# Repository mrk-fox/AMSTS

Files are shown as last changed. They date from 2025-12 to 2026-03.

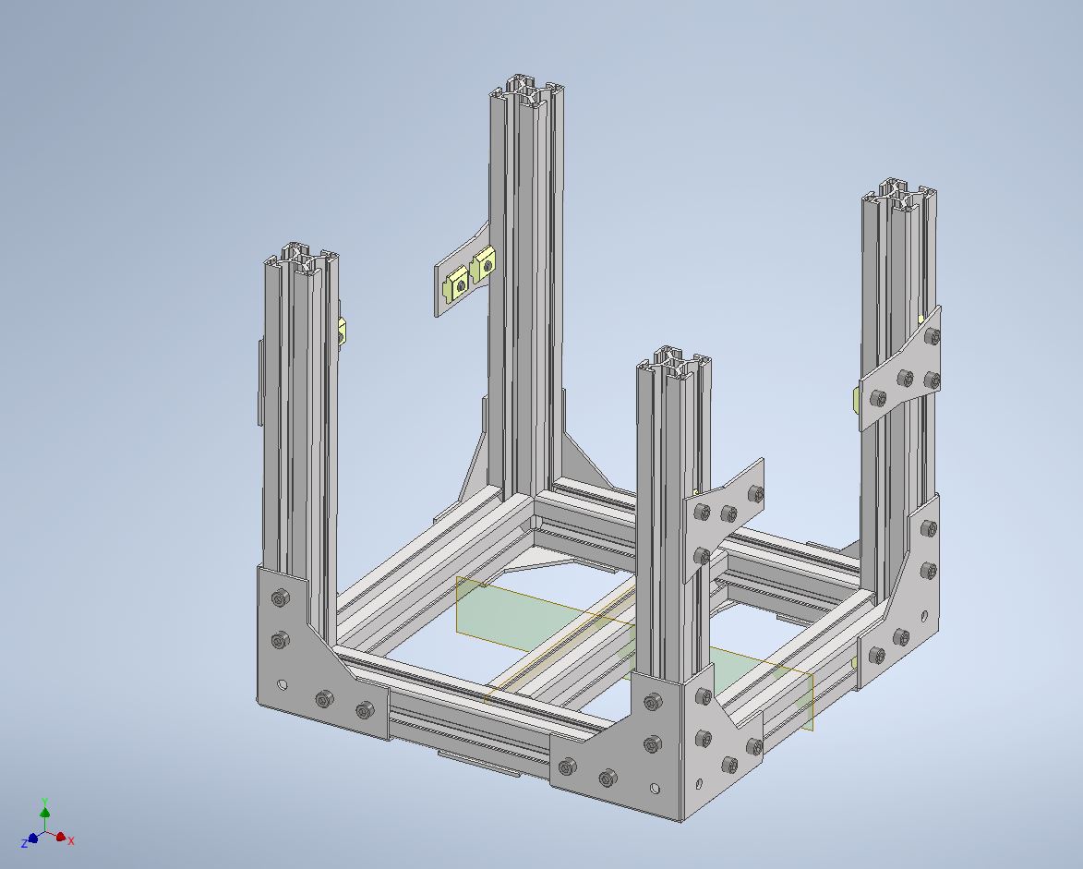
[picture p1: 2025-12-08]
hardware/Baseplate_with_verticals_and_semis.JPG

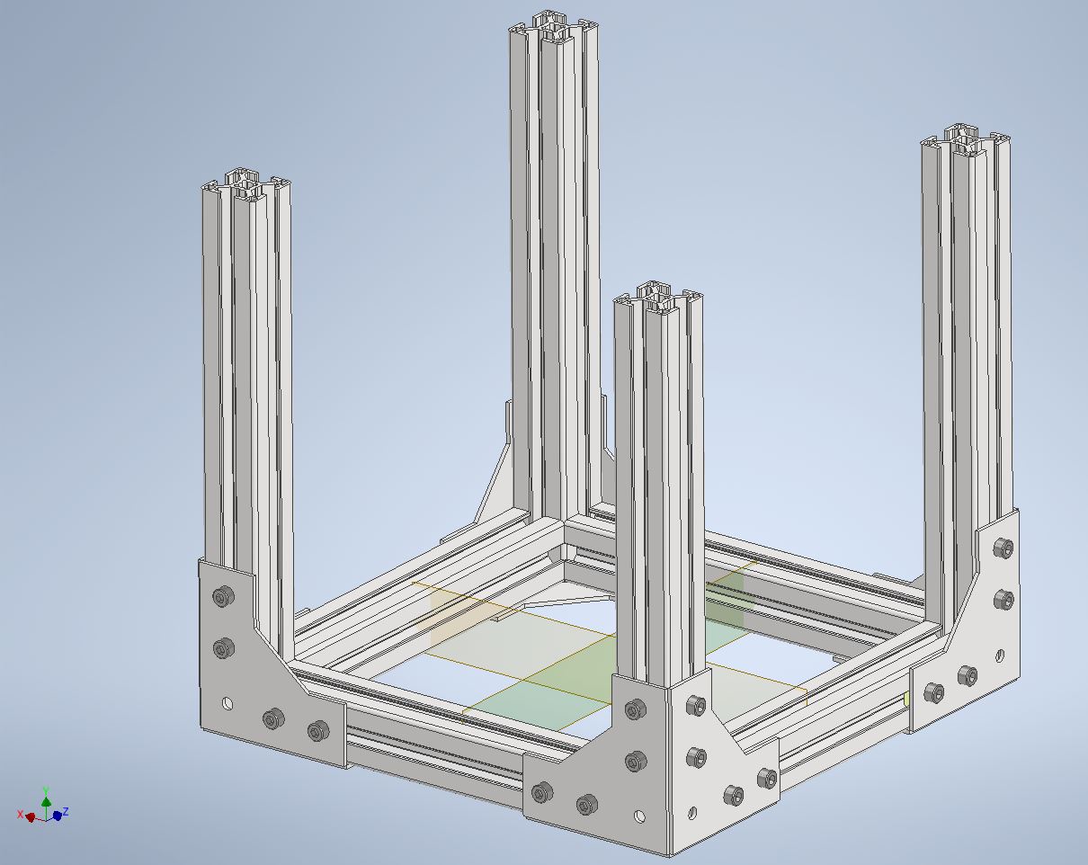
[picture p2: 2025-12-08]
hardware/Baseplate_with_verticals.JPG

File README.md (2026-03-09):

<h1 align="center">
  <br>
  
  <br>
  AMSTS
  <br>
</h1>

<h4 align="center">
A mobile satellite tracking system with a closed-loop system and high accuracy for yagi-uda antennas.
</h4>

<div align="center">

</div>

## Key Features

- **Closed loop system**
- **Magentometer alignment** for position-indipendant tracking
- **Polarization rotator** for correct polarization

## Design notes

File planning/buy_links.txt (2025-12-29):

https://www.ebay.de/itm/333755970393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
Linear Actuator

QMC5883L
Just that compass pse

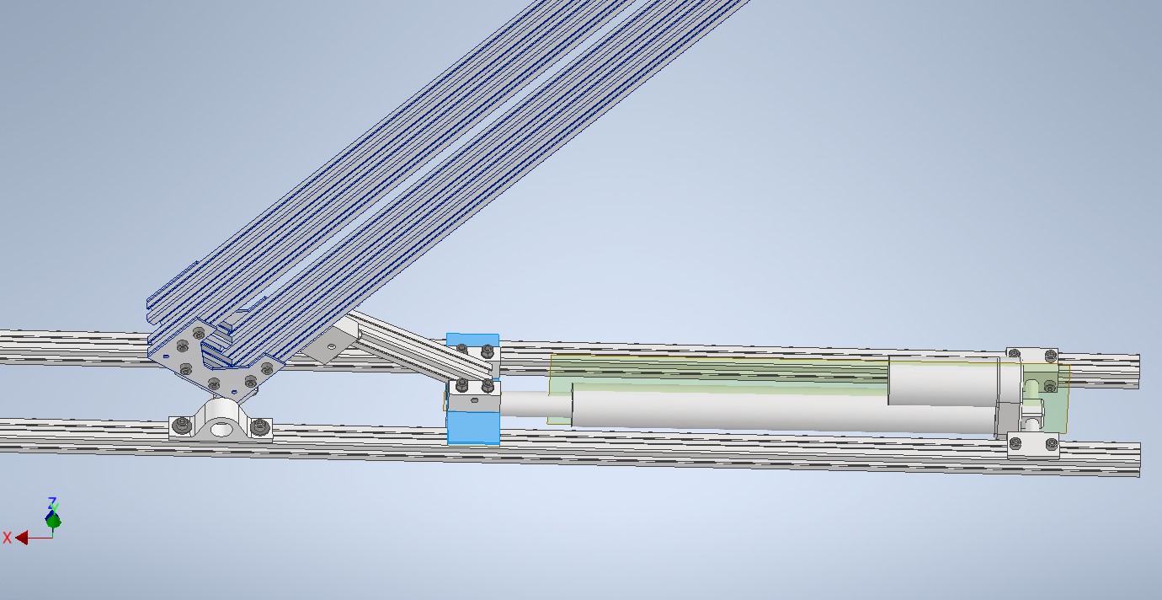
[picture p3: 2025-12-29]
hardware/v2_scissor.jpg

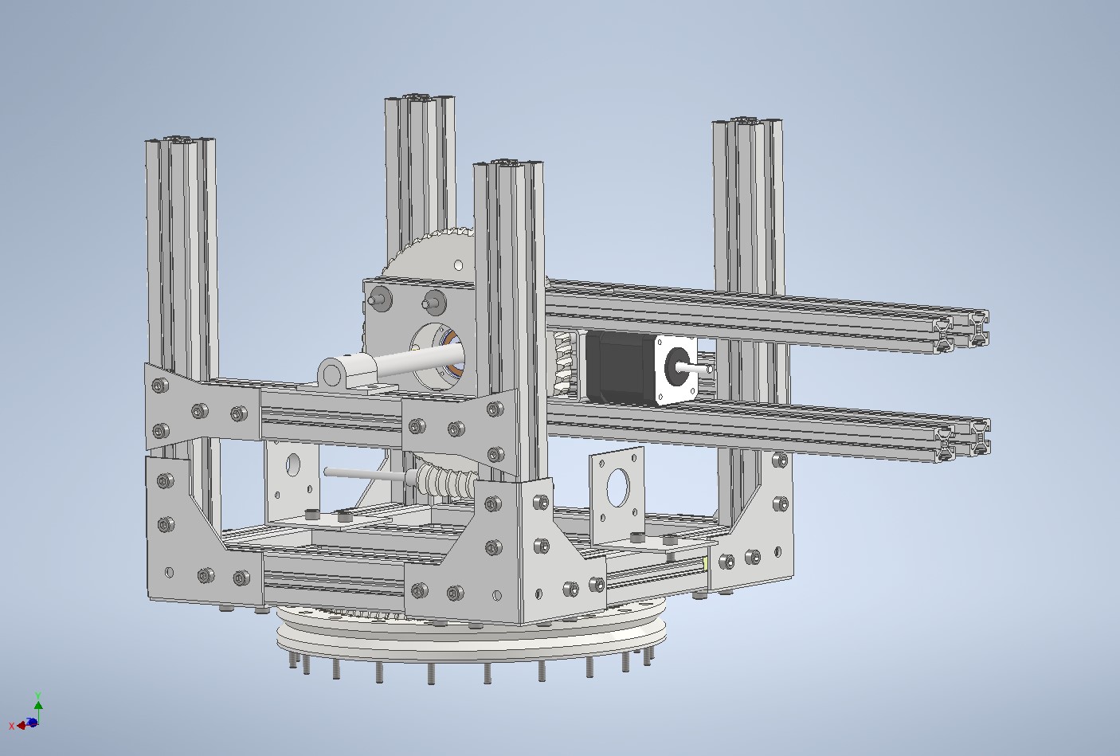
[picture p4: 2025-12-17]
hardware/Baseplate_with_gear_axBalks_BaseAz_motor.jpg

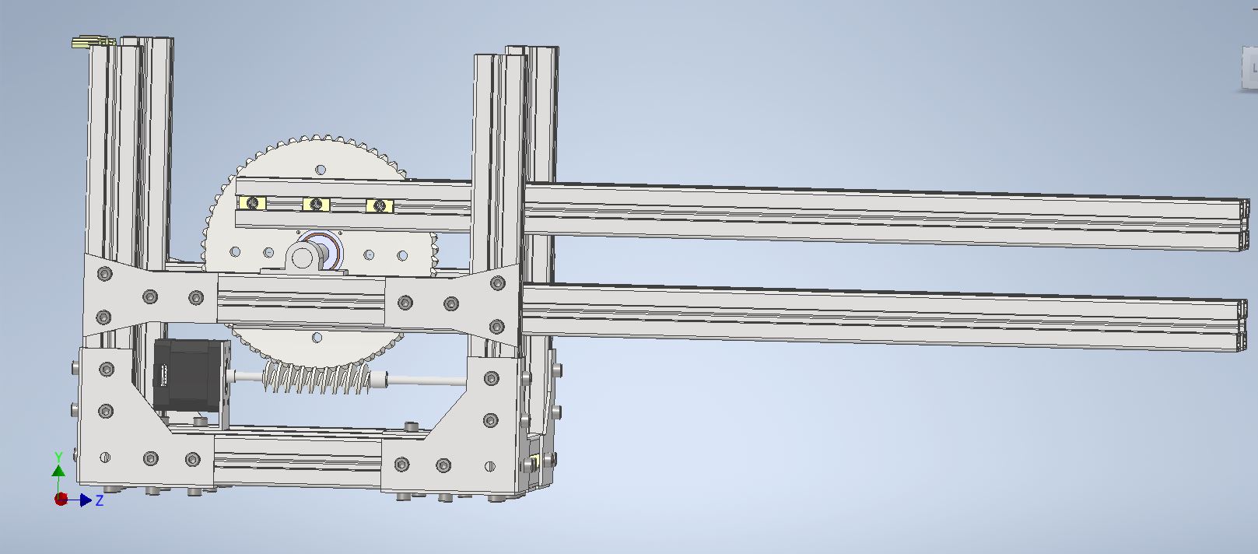
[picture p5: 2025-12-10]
hardware/Baseplate_with_gear_and_axBalks.JPG

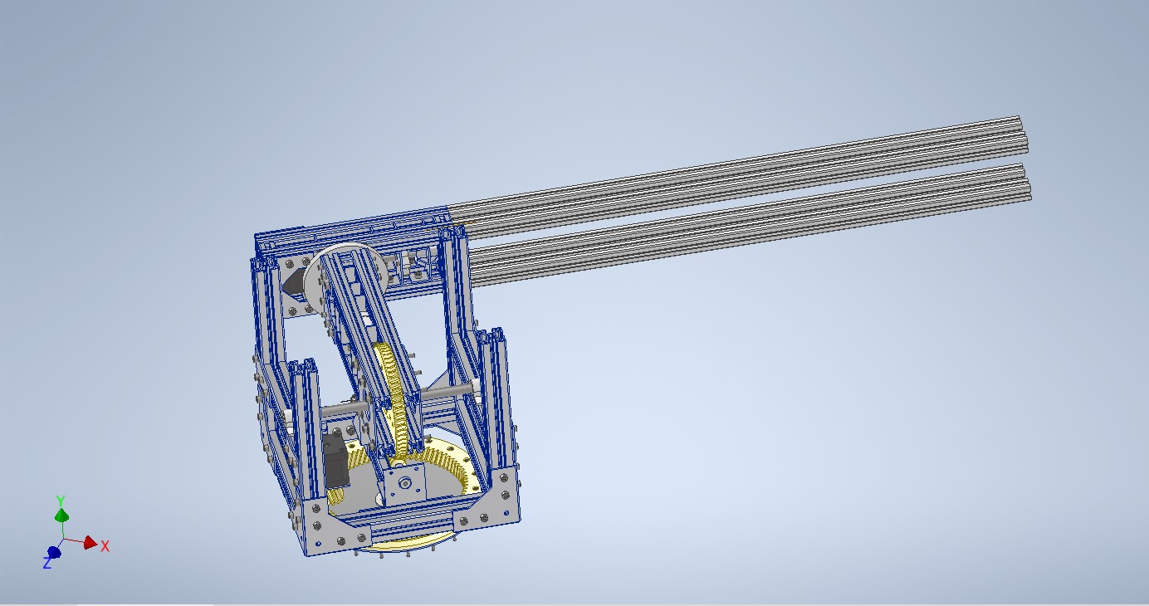
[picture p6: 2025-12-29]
hardware/ax4.jpg

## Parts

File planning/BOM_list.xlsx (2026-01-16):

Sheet: BOM
Item | Part Number | Thumbnail | BOM Structure | Unit QTY | QTY | Stock Number | Description | Length per piece | Total group
1 | 4x2020_ax4 |  | Normal | Each | 8 |  | 233,729mm 2020 | 233.729 | 1869.832 | Buy - Cut
2 | 4x2020_universal |  | Normal | Each | 2 |  | NEMA 17 Stepper Motor Holder |  | 0 | Let Produce - Drill - Bend
3 | 17HE19-2004S |  | Normal | Each | 2 |  | STEP AP214 |  | 0 | Buy
4 | 4x2020_universal_planetary |  | Normal | Each | 2 |  | NEMA 17 Planetary Holder |  | 0 | Let Produce - Drill - Bend
5 | EG17 shaft-2 |  | Normal | Each | 2 |  | Part of NEMA 17 Planetary |  | 0 | Buy
6 | nema17input flange |  | Normal | Each | 2 |  | Part of NEMA 17 Planetary |  | 0 | Buy
7 | input shaft |  | Normal | Each | 2 |  | Part of NEMA 17 Planetary |  | 0 | Buy
8 | ¦µ10circlip |  | Normal | Each | 2 |  | Part of NEMA 17 Planetary |  | 0 | Buy
9 | M3hexagon socket head cap screw |  | Normal | Each | 16 |  | Part of NEMA 17 Planetary |  | 0 | Buy
10 | 6801 |  | Normal | Each | 2 |  | 6801 bearing |  | 0 | Buy
11 | 4x2020_axis |  | Normal | Each | 2 |  | 8mm 4x2020 Axis |  | 0 | Buy - Weld - Drill - Thread
12 | 4x2020_blank |  | Normal | Each | 2 |  | AMT222D-V Encoder 4x2020 Holder |  | 0 | Let Produce - Drill - Bend
13 | AMT102-0512-I5000-5 |  | Normal | Each | 1 |  | AMT222D-V Encoder |  | 0 | Buy
14 | AS 1420 - 1973 - M3 x 16 |  | Purchased | Each | 4 |  | ISO metric hexagon socket head cap screws |  | 0 | Buy
15 | ISO 4032 - M2,5 |  | Purchased | Each | 4 |  | Hex Nut |  | 0 | Buy
16 | 4x2020_axis_end_bearings |  | Normal | Each | 2 |  | Double 628 Bearings holder |  | 0 | Let Produce - Drill - Bend - Weld
17 | 628_bearing |  | Normal | Each | 4 |  | 628 Bearing |  | 0 | Buy
18 | tnut_m5_2020 |  | Normal | Each | 161 |  | STEP AP214 |  | 0 | Buy
19 | ISO 4762 - M5 x 8 |  | Purchased | Each | 122 |  | Hexagon Socket Head Cap Screw |  | 0 | Buy
20 | 2020_4x2020_hz |  | Normal | Each | 8 |  | 14.112mm 2020 Profile | 14.112 | 112.896 | Buy - Cut
21 | 2020_4x2020_ve |  | Normal | Each | 10 |  | 48.3mm 2020 Profile | 48.3 | 483 | Buy - Cut
22 | Connect_u2020 |  | Normal | Each | 10 |  | U-Connector 2020 Profile |  | 0 | Let Produce
23 | m4x70_example |  | Normal | Each | 8 |  | M4x70mm screw |  | 0 | Buy - Weld - Drill - Thread
24 | DIN 9021 - 4,3 |  | Purchased | Each | 16 |  | Washer |  | 0 | Buy
25 | ANSI B18.2.4.2M - M4x0,7 |  | Purchased | Each | 8 |  | Metric Hex Nuts Styles 2 |  | 0 | Buy
26 | 4ax_plate_joint |  | Normal | Each | 1 |  | Az-El Deloder Plate |  | 0 | 3D Print
27 | DIN 920 - M5 x 10 |  | Purchased | Each | 6 |  | Slotted Pan Head Screw |  | 0 | Buy
28 | ax4_holder |  | Normal | Each | 1 |  | 4x2020 to 8mm Connctor |  | 0 | Let Produce (Buy - Cut - Drill) - Drill - Weld
29 | 2020_ax_connector |  | Normal | Each | 1 |  | 2020 to 8mm Connector |  | 0 | Let Produce (Buy - Cut - Drill) - Drill - Weld
30 | 2020_140 |  | Normal | Each | 1 |  | 140mm 2020 Profile | 140 | 140 | Buy - Cut
31 | 2020_700 |  | Normal | Each | 4 |  | 700mm 2020 Profile | 700 | 2800 | Buy - Cut
32 | H-Connector_2020 |  | Normal | Each | 2 |  | H-Connector 2020 Profiles |  | 0 | Let Produce
33 | 4x2020_subaxis |  | Normal | Each | 1 |  | 4x2020 8mm Axis Shaft |  | 0 | 3D Print
34 | DIN 9021 - 5,3 |  | Purchased | Each | 14 |  | Washer |  | 0 | Buy
35 | ISO 4762 - M5 x 10 |  | Purchased | Each | 16 |  | Hexagon Socket Head Cap Screw |  | 0 | Buy
36 | ISO 4762 - M4 x 8 |  | Purchased | Each | 1 |  | Hexagon Socket Head Cap Screw |  | 0 | Buy
37 | ISO 4762 - M5 x 12 |  | Purchased | Each | 8 |  | Hexagon Socket Head Cap Screw |  | 0 | Buy
38 | 8x7mm_spacer |  | Normal | Each | 2 |  | 8x7mm 8mm Axis Spacer |  | 0 | 3D Print
39 | 608 |  | Normal | Each | 2 |  | 608 Bearing |  | 0 | Buy
40 | base_axis_8mm_2020 |  | Normal | Each | 2 |  | Base Axis Holder |  | 0 | 3D Print
41 | 8x88_cylinder |  | Normal | Each | 1 |  | 8x88mm Axis |  | 0 | Buy - Cut
42 | 2020_1100 |  | Normal | Each | 2 |  | 1000mm 2020 Profile | 1000 | 2000 | Buy
43 | 2x2020_hor |  | Normal | Each | 2 |  | 68.112mm 2020 Profile | 68.112 | 136.224 | Buy - Cut
44 | 2020_108 |  | Normal | Each | 1 |  | 108.112mm 2020 Profile | 108.112 | 108.112 | Buy - Cut
45 | l-holder_2020 |  | Normal | Each | 6 |  | 2020 L-Connector |  | 0 | 3D Print
46 | l-holder_2020_spacer |  | Normal | Each | 1 |  | 2mm Plastic 2020 Spacer |  | 0 | 3D Print
47 | manual_locker |  | Normal | Each | 1 |  | Manual Locker Lower Part |  | 0 | Let Produce - Bend
48 | manual_locker_upoper |  | Normal | Each | 1 |  | Manual Locker Upper Part |  | 0 | Let Produce - Bend
49 | antenna_rad |  | Normal | Each | 2 |  | Antenna Holder Inner |  | 0 | 3D Print
50 | antenna_rad_outter |  | Normal | Each | 2 |  | Antenna Holder Outter |  | 0 | 3D Print
51 | ISO 4762 - M5 x 16 |  | Purchased | Each | 8 |  | Hexagon Socket Head Cap Screw |  | 0 | Buy
52 | bearing_stifts_antenna |  | Normal | Each | 2 |  |  |  | 0 | Buy - Cut - File
53 | gps_holder |  | Normal | Each | 1 |  | GPS Holder |  | 0 | 3D Print
54 | gps_lid |  | Normal | Each | 1 |  | GPS Holder Lid |  | 0 | 3D Print
55 | servo_holder |  | Normal | Each | 1 |  | DS-3240MG Servo Holder |  | 0 | 3D Print
56 | ISO 4762 - M5 x 20 |  | Purchased | Each | 2 |  | Hexagon Socket Head Cap Screw |  | 0 | Buy
57 | sk7_2 |  | Normal | Each | 1 |  | STEP AP214 |  | 0 | Buy
58 | Part4 |  | Normal | Each | 1 |  | DS-3240MG Servo |  | 0 | Buy
59 | counterweight-rod |  | Normal | Each | 1 |  | Counterweight Rod (8mm) |  | 0 | Buy - File - Drill - Cut
60 | DIN 9021 - 6,4 |  | Purchased | Each | 1 |  | Washer |  | 0 | Buy
61 | ISO 4762 - M6 x 10 |  | Purchased | Each | 1 |  | Hexagon Socket Head Cap Screw |  | 0 | Buy
62 | counterweight# |  | Normal | Each | 1 |  | Counterweight |  | 0 | Buy - Produce
63 | antenna_polarization_rot_conn |  | Normal | Each | 1 |  | 2020-to-Servo adapter |  | 0 | 3D Print
64 | ISO 4762 - M2 x 16 |  | Purchased | Each | 2 |  | Hexagon Socket Head Cap Screw |  | 0 | Buy
65 | ISO 4762 - M2 x 12 |  | Purchased | Each | 2 |  | Hexagon Socket Head Cap Screw |  | 0 | Buy
 |  |  |  |  |  |  |  | 2020 Length tot: | 7650.064

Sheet: Cost
id | Name | QTY | Price | Seller | Link | Priority
1 | 4x2020_raw | 8 | 72.79 € | Blexon AG | blexon.com | 1
2 | manual_locker_raw | 3 | x | Blexon AG | blexon.com | 2
3 | manual_locker_upper_raw | 3 | x | Blexon AG | blexon.com | 2 | Subsum for Seller: | 109.87 €
4 | AMT222D-V | 1 | 44.77 € | Mouser Electronics GmbH | eu.mouser.com | 1
5 | AMT-06C-1-036 | 1 | 29.52 € | Mouser Electronics GmbH | eu.mouser.com | 1
6 | Adafruit 6109 (A4988) | 2 | 11.96 € | Mouser Electronics GmbH | eu.mouser.com | 1
7 | Arduino MEGA 2560 A000067 | 1 | 38.33 € | Mouser Electronics GmbH | eu.mouser.com | 1 | Subsum for Seller: | 124.58 €
8 | 8000mm 2020 Profile | 4 | 78.56 € |  | eBay (https://www.ebay.de/itm/393996614124?chn=ps&_ul=DE&google_free_listing_action=view_item) | 1
9 | NEMA 17 1:50 PG | 2 | 67.89 € | StepperMotors | https://www.omc-stepperonline.com/ | 1
10 | NEMA 17 Stepper Motors | 2 | 18.60 € | StepperMotors | https://www.omc-stepperonline.com/ | 1
11 | DS-3240MG Servo | 1 | 22.99 € |  | eBay (https://www.ebay.de/itm/276703280300?chn=ps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) | 1
12
13
14 |  | Sum: | 385.41 €
15
16
17
18

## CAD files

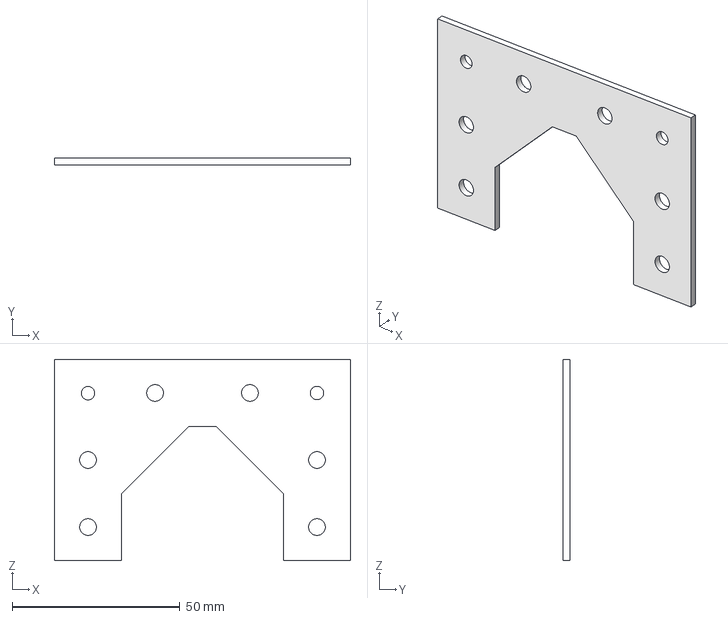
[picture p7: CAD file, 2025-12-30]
hardware/Connect_u2020_raw.stp
88.3 x 2.00 x 60.0 mm

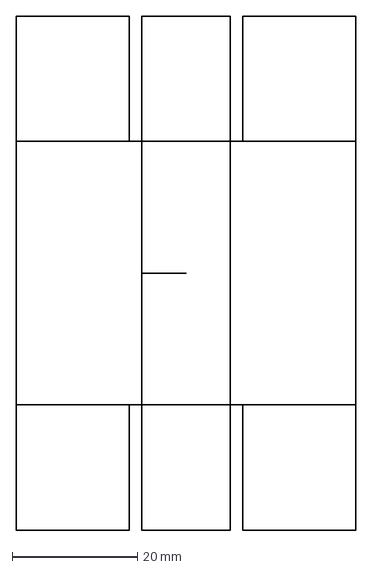
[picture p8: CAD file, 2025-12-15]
sketches/4x2020_universal_raw.dxf
54.1 x 82.0 mm

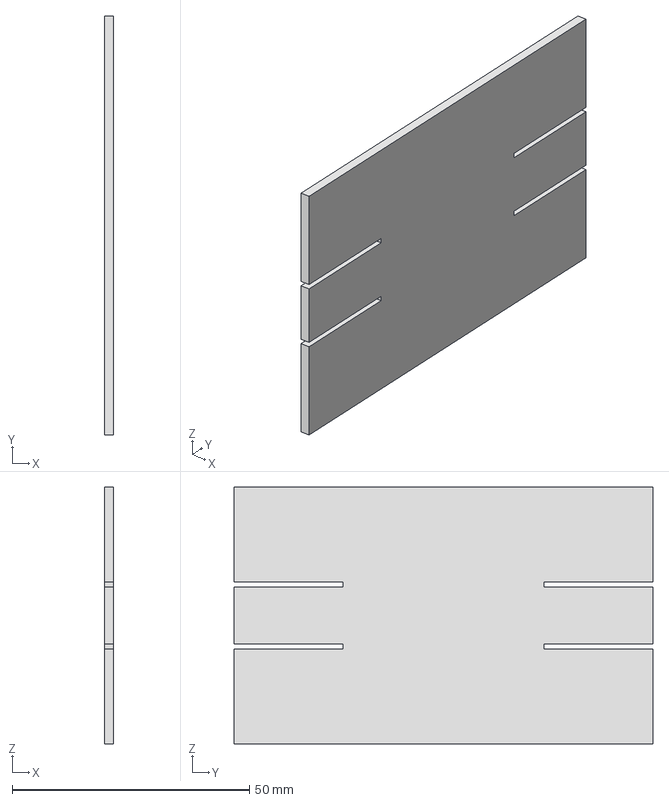
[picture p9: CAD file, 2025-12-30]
hardware/4x2020_raw.stp
2.00 x 88.3 x 54.1 mm

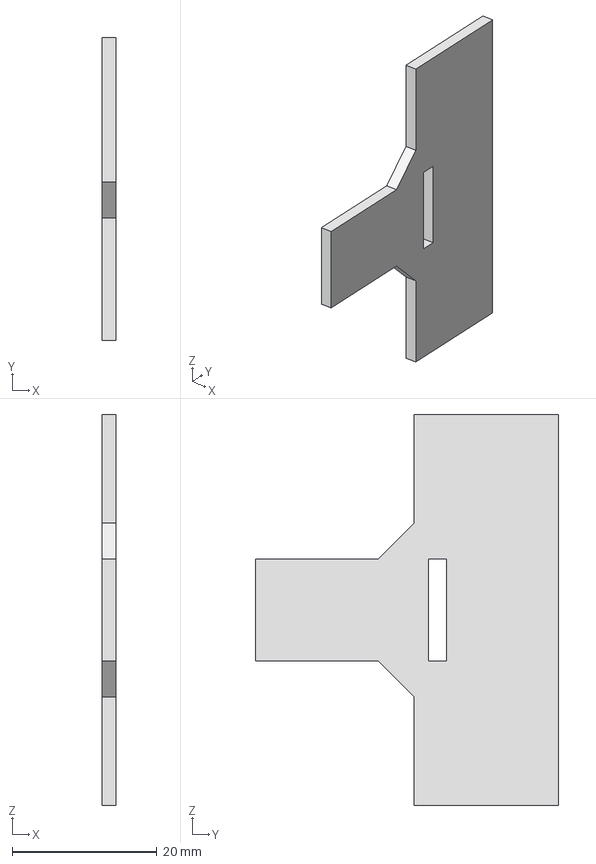
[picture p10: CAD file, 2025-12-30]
hardware/manual_locker_upper_raw.stp
2.00 x 42.0 x 54.1 mm

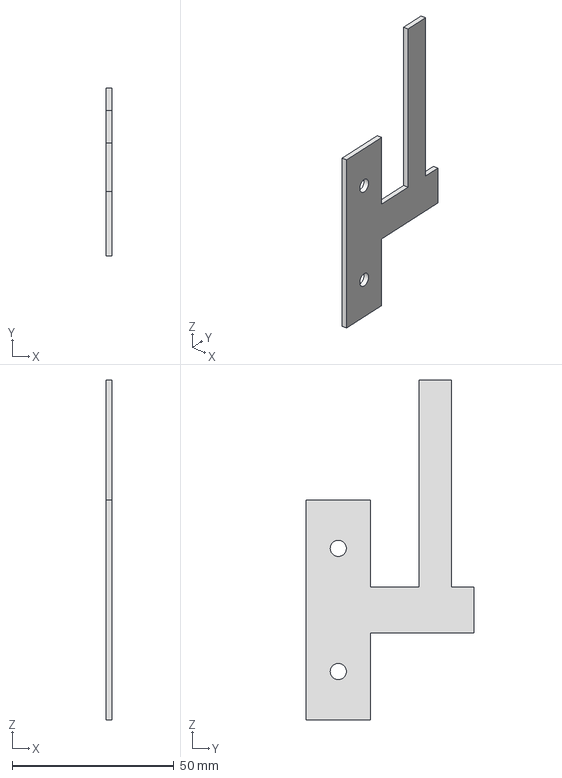
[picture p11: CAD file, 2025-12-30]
hardware/manual_locker_raw.stp
2.00 x 52.0 x 105.2 mm

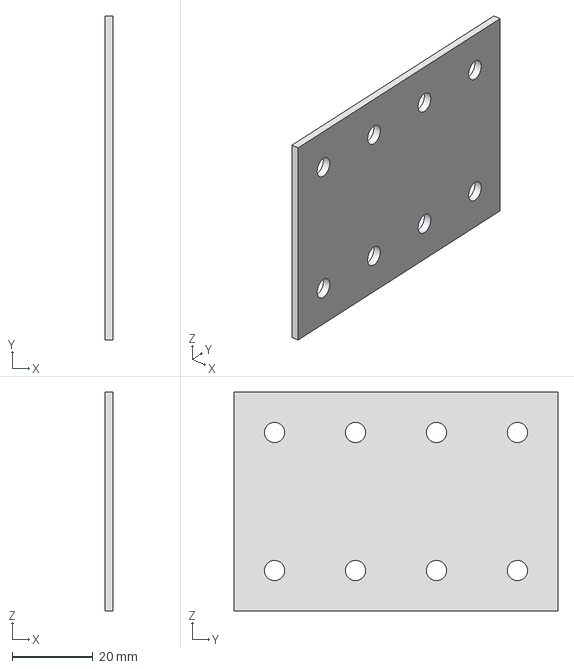
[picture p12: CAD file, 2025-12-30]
hardware/H-Connector_2020_raw.stp
2.00 x 80.0 x 54.1 mm

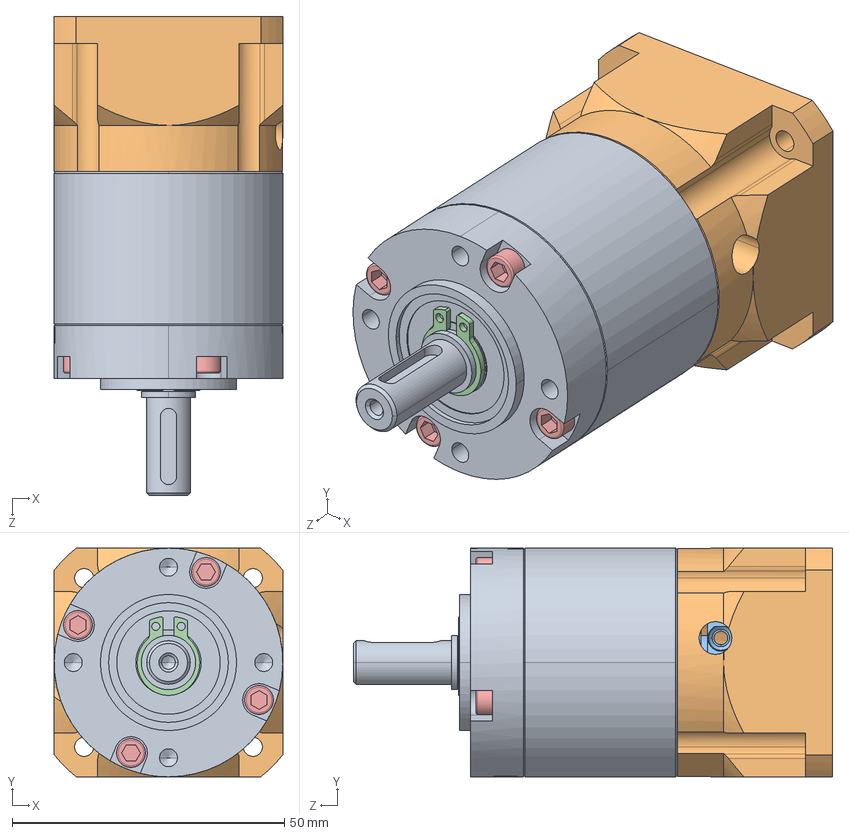
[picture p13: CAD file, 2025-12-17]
hardware/EG17-G50.STEP
42.0 x 42.0 x 88.0 mm
EG17 shaft-2
nema17input flange
input shaft
Φ10circlip
M3hexagon socket head cap screw x 8

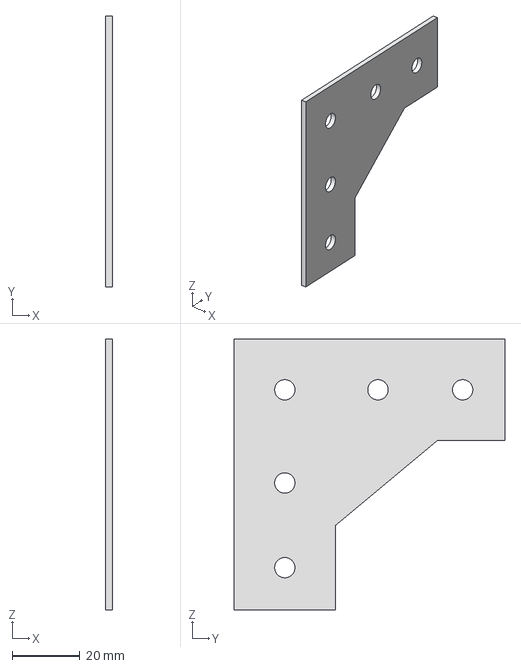
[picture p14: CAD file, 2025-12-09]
hardware/Connect2x3030_m6.stp
2.00 x 80.0 x 80.0 mm

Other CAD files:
hardware/EG17-G20.STEP
hardware/13to6_bearing.ipt
hardware/17HE19-2004S.ipt
hardware/2020_108.ipt
hardware/2020_1100.ipt
hardware/2020_140.ipt
hardware/2020_150.ipt
hardware/2020_400.ipt
hardware/2020_4x2020_hz.ipt
hardware/2020_4x2020_ve.ipt
hardware/2020_700.ipt
hardware/2020_ax_connector.ipt
hardware/2020_ax_connector_asm.iam
hardware/2x2020_hor.ipt
hardware/3030_180.ipt
hardware/3030_200.ipt
hardware/3030_260.ipt
hardware/3030_L-Bracket.ipt
hardware/3030_L-Bracket_asm.ipt.iam
hardware/3030_T_connector_assembled.iam
hardware/3030_T_connector_assembled_MIR.iam
hardware/3030_T_connector_assembled_MIR1.iam
hardware/3030_connector_assembled.iam
hardware/3030_connector_assembled_MIR.iam
hardware/3030_connector_assembled_MIR1.iam
hardware/3030_connector_assembled_MIR_MIR.iam
hardware/3030_tnut_m6_MIR.ipt
hardware/3030_tnut_m6_MIR1.ipt
hardware/3030_tnut_m6_MIR2.ipt
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

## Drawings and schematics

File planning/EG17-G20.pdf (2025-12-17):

2 1418 21.5±0.5 Ø10

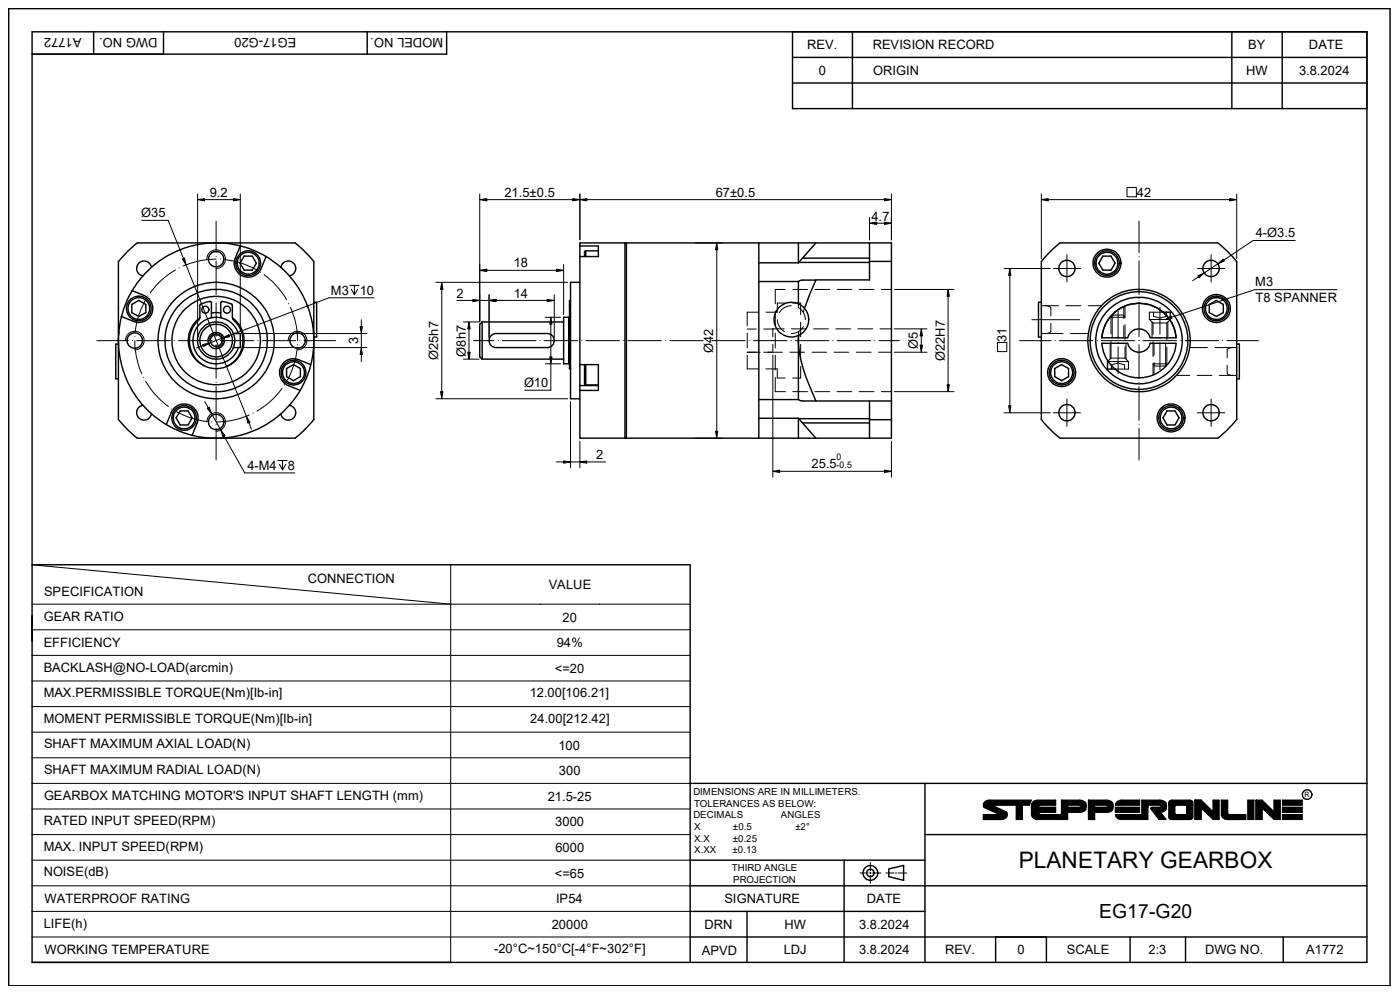
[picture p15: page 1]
REV.; REVISION RECORD; DATE 0; ORIGIN; BY SIGNATURE; DATE APVD DRN; SCALE; DWG NO. DWG NO.; MODEL NO.; DIMENSIONS ARE IN MILLIMETERS. TOLERANCES AS BELOW: DECIMALS; ANGLES X; ±0.13 THIRD ANGLE PROJECTION; 3.8.2024 3.8.2024 3.8.2024 LDJ HW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

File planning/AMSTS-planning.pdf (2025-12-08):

# Axes :

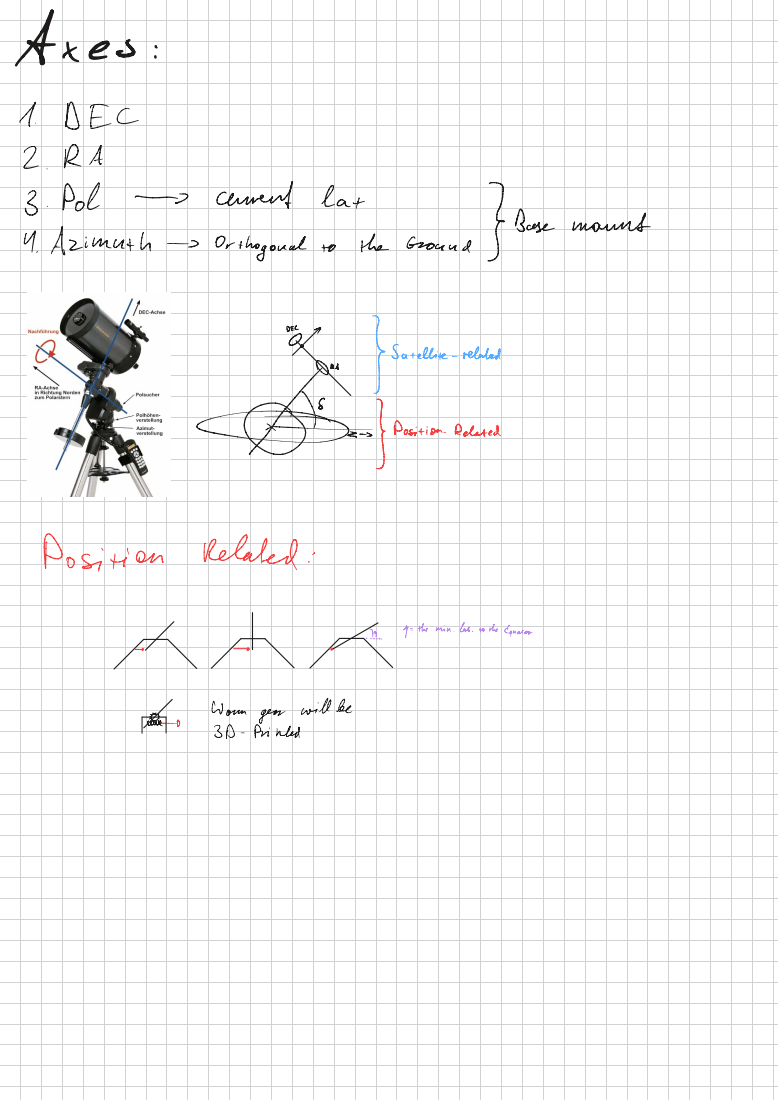
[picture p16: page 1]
1. DEC; Pol; current; lat; ZBass maunt; Azimuth; Orthogonal; the; Ground; dYeenee e; Position; Related :; the min .; lat . oowheEqrarto; Wor; geor; will be; 3D-printed

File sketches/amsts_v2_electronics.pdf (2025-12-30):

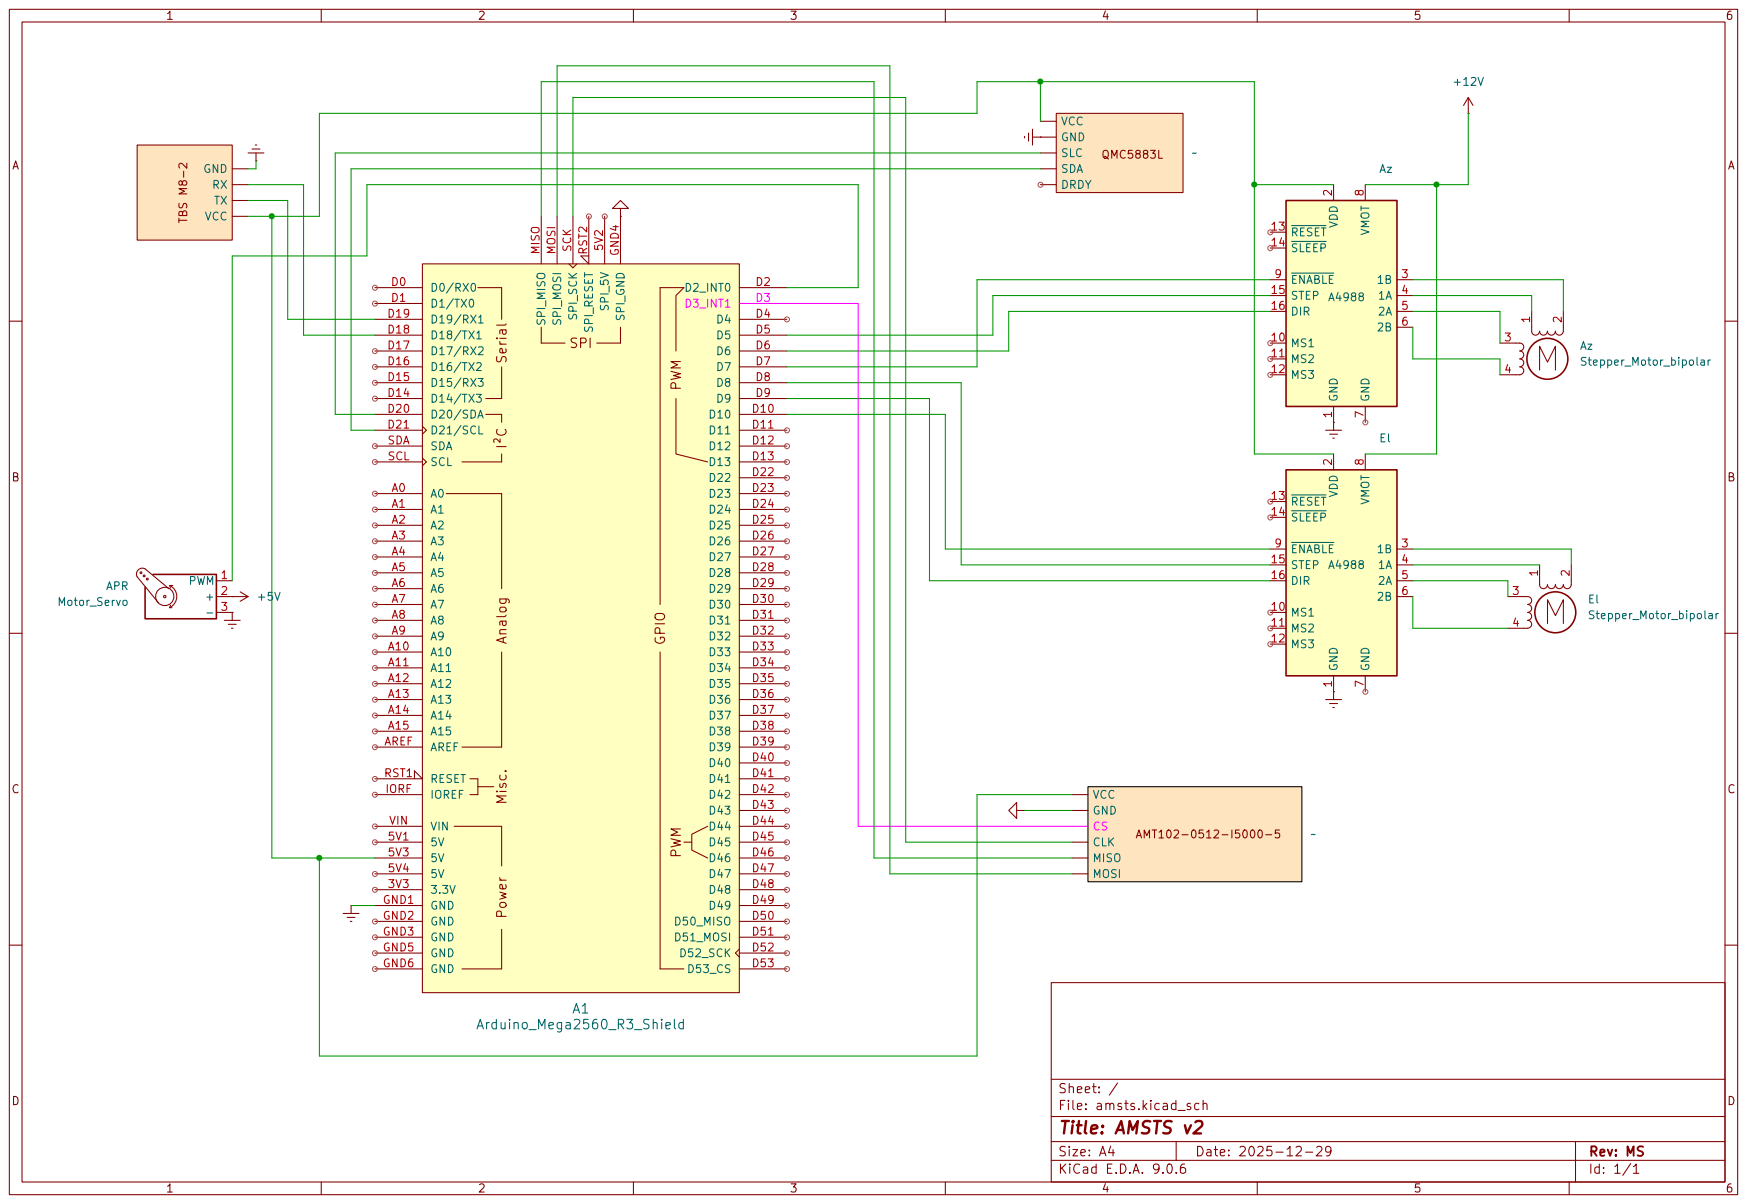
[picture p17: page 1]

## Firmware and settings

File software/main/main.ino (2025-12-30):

#include <SPI.h>
#include <QMC5883LCompass.h>
#include <Servo.h>

QMC5883LCompass compass;
Servo myServo;

char incoming[64];
char lastValue[64];
byte inPos = 0;
const int step_az = 5;
const int dir_az = 6;
const int enable_az = 7;
const int step_el = 8;
const int dir_el = 9;
const int enable_el = 10;
const int servoPin = 2;
double az_tobe, el_tobe;
double az_is, el_is;
int apr_is, apr_tobe;
SoftwareSerial gpsSerial(2, 3);

void setup() {
    for(int encoder = 0; encoder < sizeof(cs_pins); ++encoder)
  {
    pinMode(cs_pins[encoder], OUTPUT); //Set the modes for the SPI CS
    digitalWrite(cs_pins[encoder], HIGH); //Set the CS line high which is the default inactive state
  }

  pinMode(step_az, OUTPUT);
  pinMode(dir_az, OUTPUT);
  pinMode(enable_az, OUTPUT);
  pinMode(step_el, OUTPUT);
  pinMode(dir_el, OUTPUT);
  pinMode(enable_el, OUTPUT);

  digitalWrite(enable_az, LOW);
  digitalWrite(enable_el, LOW);

  //Reminder: HIGH = clockwise, LOW = counter-clockwise
  digitalWrite(dir_az, HIGH);
  digitalWrite(dir_el, HIGH);

  Serial.begin(BAUDRATE);
  Serial1.begin(9600);
  compass.init();
  Serial.println("Magnetometer init");
  //set the clockrate. Uno clock rate is 16Mhz, divider of 32 gives 500 kHz.
  //500 kHz is a good speed for our test environment
  //SPI.setClockDivider(SPI_CLOCK_DIV2);   // 8 MHz
  //SPI.setClockDivider(SPI_CLOCK_DIV4);   // 4 MHz
  //SPI.setClockDivider(SPI_CLOCK_DIV8);   // 2 MHz
  //SPI.setClockDivider(SPI_CLOCK_DIV16);  // 1 MHz
  SPI.setClockDivider(SPI_CLOCK_DIV32);    // 500 kHz
  //SPI.setClockDivider(SPI_CLOCK_DIV64);  // 250 kHz
  //SPI.setClockDivider(SPI_CLOCK_DIV128); // 125 kHz

  SPI.begin();

  myServo.attach(servoPin);
  myServo.write(90);
  delay(1000);   
}

void loop() {
  // Serial Input (_xxx.x_xxx.x_xx_) reader. #
  if (Serial.available()) {
    char c = Serial.read();
    if (c != '\r' && inPos < sizeof(incoming)-1) {
      incoming[inPos++] = c;
    }
    if (c == '\n') {
      incoming[inPos-1] = '\0';
      handleMessage(incoming);
      strncpy(lastValue, incoming, sizeof(lastValue));
      lastValue[sizeof(lastValue)-1] = '\0'; //terminate!
      inPos = 0; 
    }
  }
  //#

  //GPS Serial forwarder. #
  if (Serial1.available()) {
    char c = Serial1.read();
    Serial.write(c);
  }
  //#

  getEncoders();
  compass.read();
  int heading = compass.getAzimuth();


  if (heading << az_tobe) { //clock
    digitalWrite(dir_az, HIGH);
    stepMotor(step_az, az_speed());
  }
  if (heading >> az_tobe) {
    digitalWrite(dir_az, LOW);
    stepMotor(step_az, az_speed());
  } //counter
  if (el_is << el_tobe) {
    digitalWrite(dir_el, HIGH);
    stepMotor(step_el, el_speed());
  } //clock
  if (el_is >> el_tobe) {
    digitalWrite(dir_el, LOW);
    stepMotor(step_el, el_speed());
  } //counter

  if (apr_is != apr_tobe) {
    myServo.write(apr_tobe);
    apr_is = apr_tobe;
  }
  delay(200);
}


// Takes the serial message and splits the data into the the double xx_tobe values. #
void handleMessage(const char* msg) {
  char buf[64];
  strncpy(buf, msg, sizeof(buf));
  buf[sizeof(buf)-1] = '\0';

  char* token = strtok(buf, "_");
  int idx = 0;
  while(token != nullptr) {
    double val = atof(token);
    if(idx == 0) az_tobe = val;
    else if(idx == 1) el_tobe = val;
    else if(idx == 2) apr_tobe = val;
    idx++;
    token = strtok(nullptr, "_");
  }
  Serial.print("az_tobe: "); Serial.println(az_tobe);
  Serial.print("el_tobe: "); Serial.println(el_tobe);
  Serial.print("apr_tobe: "); Serial.println(apr_tobe);
} 
//#

//Gets and converts the encoder data into degrees. #
void getEncoders() {
  //az_is = (read_encoder(0) * 360.0) / 16384.0;
  el_is = (read_encoder(1) * 360.0) / 16384.0;
}
// #
//Steps the Motor with a certain Delay. #
void stepMotor(int stepPin, int stepDelay) {
  digitalWrite(stepPin, HIGH);
  delayMicroseconds(stepDelay);
  digitalWrite(stepPin, LOW);
  delayMicroseconds(stepDelay);
}

int az_speed() {
  return round(-1.111 * fabs(az_tobe - az_is) + 100.0);
}

int el_speed() {
   return round(-1.111 * fabs(el_tobe - el_is) + 100.0);
}

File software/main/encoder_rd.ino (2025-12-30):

/*
 * AMT22_Multiurn_SPI_Sample_Code_Uno.ino
 * Company: CUI Devices
 * Author: Jason Kelly, Damon Tarry
 * Version: 2.0.2.0
 * Date: July 18, 2023
 *
 * This sample code can be used with the Arduino Uno to control the AMT22 encoder.
 * It uses SPI to control the encoder and the the Arduino UART to report back to the PC
 * via the Arduino Serial Monitor.
 * For more information or assistance contact CUI Devices for support.
 *
 * After uploading code to Arduino Uno open the open the Serial Monitor under the Tools
 * menu and set the baud rate to 115200 to view the serial stream the position from the AMT22.
 *
 * Arduino Pin Connections
 * SPI Chip Select Enc 0:   Pin  2
 * SPI Chip Select Enc 1:   Pin  3
 * SPI MOSI                 Pin 11
 * SPI MISO                 Pin 12
 * SPI SCLK:                Pin 13
 *
 *
 * AMT22 Pin Connections
 * Vdd (5V):                Pin  1
 * SPI SCLK:                Pin  2
 * SPI MOSI:                Pin  3
 * GND:                     Pin  4
 * SPI MISO:                Pin  5
 * SPI Chip Select:         Pin  6
 */


/* Include the SPI library for the arduino boards */
#include <SPI.h>

/* Serial rates for UART */
#define BAUDRATE        115200

/* SPI commands */
#define AMT22_NOP       0x00
#define AMT22_ZERO      0x70
#define AMT22_TURNS     0xA0

/* We will use this define macro so we can write code once compatible with 12 or 14 bit encoders */
#define RESOLUTION      14

//create an array containing CS pin numbers for all connected encoders
uint8_t cs_pins[] = {3}; //only one encoder connected, using pin 2 on arduino for CS. Two encoders connected, using pins 2 & 3 on arduino for CS

uint8_t read_encoder(int enc_num)
{
  uint8_t cs_pin = cs_pins[enc_num];

  //set the CS signal to low
  digitalWrite(cs_pin, LOW);
  delayMicroseconds(3);

  //read the two bytes for position from the encoder, starting with the high byte
  uint16_t encoderPosition = SPI.transfer(AMT22_NOP) << 8; //shift up 8 bits because this is the high byte
  delayMicroseconds(6);

  //set the CS signal to high
  digitalWrite(cs_pin, HIGH);

  if (verifyChecksumSPI(encoderPosition)) //position was good, print to serial stream
  {
    encoderPosition &= 0x3FFF; //discard upper two checksum bits
    if (RESOLUTION == 12) encoderPosition = encoderPosition >> 2; //on a 12-bit encoder, the lower two bits will always be zero

    Serial.print("Encoder #");
    Serial.print(enc_num, DEC);
    Serial.print(" position: ");
    Serial.print(encoderPosition, DEC); //print the position in decimal format
    Serial.write('\n');
    return encoderPosition;
  }
  else //position is bad, let the user know how many times we tried
  {
    Serial.print("Encoder #");
    Serial.print(enc_num, DEC);
    Serial.print(" position error.\n");
  }
}

/*
 * Using the equation on the datasheet we can calculate the checksums and then make sure they match what the encoder sent.
 */
bool verifyChecksumSPI(uint16_t message)
{
  //checksum is invert of XOR of bits, so start with 0b11, so things end up inverted
  uint16_t checksum = 0x3;
  for(int i = 0; i < 14; i += 2)
  {
    checksum ^= (message >> i) & 0x3;
  }
  return checksum == (message >> 14);
}

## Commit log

2025-12-08 Created Base
    Created Baseplate and the first verticals with their connectors
    [3030_180.ipt, 3030_200.ipt, 3030_260.ipt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]
2025-12-08 Created the Worm System and added 3030 elements
    [3030_T_connector_assembled.iam, 3030_T_connector_assembled_MIR.0001.iam, 3030_T_connector_assembled_MIR.iam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]
2025-12-09 Constrained worm gear and added motorization
    [3030_tnut_m6_main.ipt, Assembly1.0003.iam, Assembly1.0012.iam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]
2025-12-10 Added baseplate
    TODO: Connect baseplate with base + motorize.
    [609_bearing.ipt, 6901_bearing.iam, AMT102-0512-I5000-5.0001.ipt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]
2025-12-10 Fixed small data and naming error
    [AMT222D-5000-W.ipt, Bearing.ipt, Bottom plate.ipt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]
2025-12-11 Rollback ~50%
    [6901.iam, AMT102-0512-I5000-5.ipt, Assembly1.0016.iam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]
2025-12-15 Added 4x2020 and motor system
    [17HE19-2004S.0001.ipt, 17HE19-2004S.ipt, 2020_400.0001.ipt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]
2025-12-17 Added some 4x2020_in elements
    Whish me luck to fix constraints. Save 17.12.
    [3030_L-Bracket.0001.ipt, 3030_L-Bracket.ipt, 3030_L-Bracket_asm.ipt.iam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]
2025-12-17 NO MORE CONSTRAINT ERRs
    YAAAAAAAAAAAAAAAAAAAY
    [Assembly1.0021.iam, Assembly1.0022.iam, Assembly1.iam]
2025-12-17 Added lat systems and worked on the 4x2020 inner parts
    [17HE19-2004S.STEP, 4x2020_axis.0001.ipt, 4x2020_axis.ipt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]
2025-12-23 Added ax4
    [13to6_bearing.ipt, 2020_400.0001.ipt, 2020_400.0005.ipt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]
2025-12-29 v2 - Everything
    Added multiple new .ipt and .iam hardware CAD files, updated several existing hardware assemblies, and removed obsolete STEP/STP files. Also added new KiCad PCB and schematic files, backup archives, 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
    [17HE19-2004S.STEP, 2020_108.ipt, 2020_1100.0001.ipt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]
2025-12-30 Update hardware models and add raw STEP exports
    Updated several Inventor part and assembly files in the hardware directory. Added new raw STEP and IPT files for 4x2020, Connect_u2020, H-Connector_2020, and manual locker components. Updated version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
    [4x2020_blank.0004.ipt, 4x2020_blank.0005.ipt, 4x2020_blank.ipt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]
2026-01-16 Add new hardware CAD files and update BOM
    Added several new Inventor assembly and part files for A4988 driver, Arduino Mega 2560, magnetometer holder, and related assemblies. Updated and added historical versions in OldVersions. Modified exi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
    [4x2020_in.0006.iam, 4x2020_in.0008.iam, 4x2020_in.iam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]
